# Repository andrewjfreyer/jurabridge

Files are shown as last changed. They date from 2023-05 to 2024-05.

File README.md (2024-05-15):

# jurabridge ☕

# TL;DR

An [ESP32 dev board](https://github.com/andrewjfreyer/jurabridge/wiki/Hardware) coupled to the service port of a [Jura ENA Micro 90](https://us.jura.com/en/customer-care/products-support/ENA-Micro-90-MicroSilver-UL-15116) can (1) poll machine data (e.g., sensors, memory, settings) via UART and (2) issue commands to the machine so as to act as a bridge between the machine and Home Assistant. See here for [hardware](https://github.com/andrewjfreyer/jurabridge/wiki/Hardware) and [software](https://github.com/andrewjfreyer/jurabridge/wiki/software) requirements. [Connections are straightforward.](https://github.com/andrewjfreyer/jurabridge/wiki/Hardware#connection-diagram)

[Home Assistant Forum Link](https://community.home-assistant.io/t/jura-ena-micro-90-to-mqtt-bridge)

# Summary

ESP32 Arduino project for bridging a [Jura ENA Micro 90](https://us.jura.com/en/customer-care/products-support/ENA-Micro-90-MicroSilver-UL-15116) to home automation platforms via MQTT. A 3.3v to 5v level shifter is required between hardware UART of the ESP32 to the service port of the Jura. The ESP32 polls the Jura for status information via reverse-engineered Jura Service Port calls, calculates/determines device state and meta statuses and reports changes to an MQTT broker. Added custom preparation functionality via a separate input button.

<p align="center">
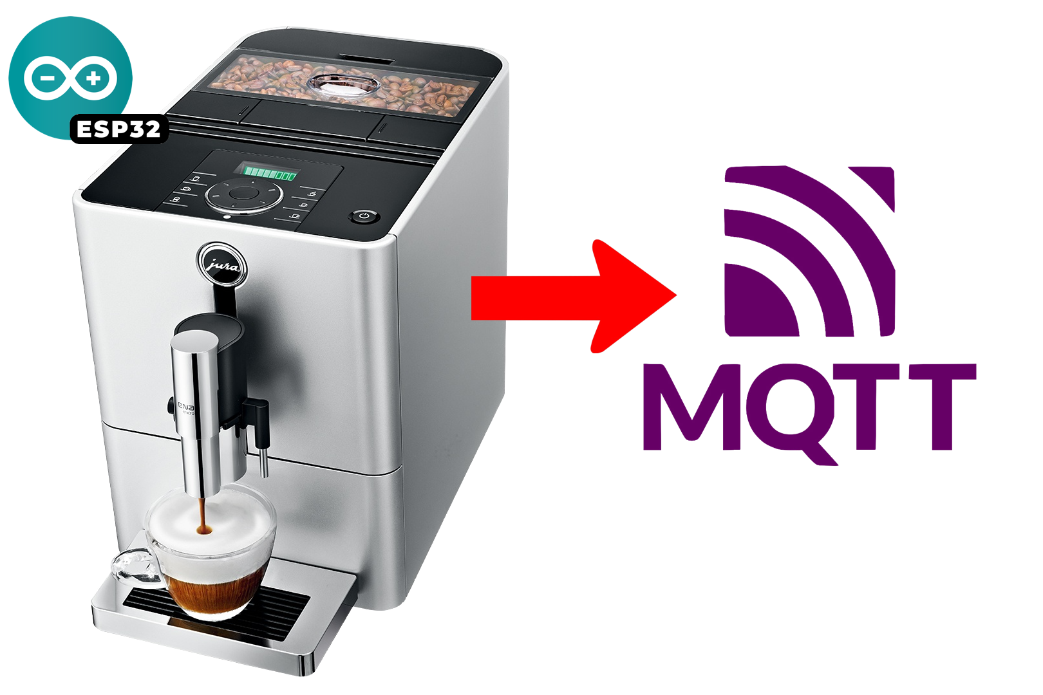
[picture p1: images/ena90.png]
Jura ENA Micro 90
  
</p>

# Why? It's a discontinued machine...

For fun, that's all. The machine is *awesome* and still available as a refurb. 

I saw [this](https://github.com/ryanalden/esphome-jura-component/) and other projects for other Jura models and thought I'd begin investigating the ENA Micro 90. Some existing comands worked, most did not. I needed to investigate and characterize a lot of the output from the machine and iterate through hundreds of commands to determine which ones the machine responded to, note what the response was, and then set about decoding/understanding what the data meant. One thing led to another, and now we're here. 

# So what? 

With 'jurabridge' we can/have: 

* ✅ **Power control.** Automatically turn the machine on and off in response to whatever triggers I want (via Home Assistant). Personally, mine is triggered from a motion sensor nearby the kitchen in the mornings. 

* ✅ **Custom coffee drinks.** Automatically create custom coffee or milk drinks with an arbitrary number of shots, arbitrary milk quantity, arbitrary water quantity (e.g., cortado, americano, lungo, ristretto, short cap, and so on). 

* ✅ **Tuning.** Fine-tune shots to improve quality. By default, the machine doses 8 - 9g of coffee (it seems) and pushes through it 30ml of water, which ends up being a 3:1 grounds to water dosing ratio. That's about half-strenth compared to a traditional pull. Also, after extraction starts, channeling is almost guaranteed to take over and extraction will suffer even before we consider how much water is being forced through. To improve shot quality then, we need to reduce water and/or increase coffee. We can't increase coffee because of torque limitations of the brew group drive motor during tamping. So our best option to improve our shot is to pull 15 - 17ml through a standard 8g puck twice, back-to-back. This would give about 30ml of espresso pulled through 16g of coffee, in aggregate. The shots are *much* better to my palate using this technique.

* ✅ **Quality control.** The thermoblock does not have fine temperture control, so there is quite a large range of possible extraction temperatures for different shots. The system can warn if the thermoblock is too high (meaning overextraction is likely), or if the thermoblock is too low (meaning underextraction is likely). In either case, running water through the machine can serve three purposes: (1) pre-warm a mug, (2) normalize thermoblock temperature below or around 100°C by purging heat or forcing the thermoblock on, and (3) clean the mug. This is not necessary in all cases, but is a good idea for best shot performance. 

* ✅ **Automation.** Automate our fine-tunings and/or temperature purge so that a perfect pull (sequence) executes without supervision.

* ✅ **Convenience & sanitation.** Automate maintenance operations such as brew group rinse and milk system rinse when the machine is idle. This will save internal silicon tubing from absorbing and accumulating burned coffee flavors, and it'll improve the sanitation of the milksystem.

* ✅ **Reminders.** Create maintence reminders or alerts via Home Assistant (e.g., iOS notifications, Alexa notifications, UI alerts or badges)

* ✅ **Alerts.** iOS alerts when a coffee product is ready.
  
* ✅ **Improved safety.** Ensure the machine turns off at an appropriate time, or in response to certain conditions. *⚠️ NOTE: If a milk clean operation is not completed and the machine is waiting for "water for milk clean," the thermoblock is held around 150 degrees celcius for sanitation purposes. There *DOES NOT* appear to be a timeout apart from the machine's power off timer, which may be on the order of hours. If the machine is left in this state, it'll consume signifiant power and pose a minor fire risk.*
  
* ✅ **Ridiculousness.** Due to the connection to Home Assisant, we have connection to voice assistants too: "Alexa, make me a short espresso." 

* ✅ **Overwhelming data.** We retreive all meters from the machine, including service life of the grinder, the drive motor of the brew group, and others. Can inform when other maintenance is necessary. 

# Table of Contents

### Reverse Engineering 

* [Jura ENA Micro 90 Command/Response Investigations & Interpretations](https://github.com/andrewjfreyer/jurabridge/wiki/Jura-Ena-Micro-90-Commands-v2)

* [Relevant Schematics](https://github.com/andrewjfreyer/jurabridge/wiki/Schematic(s))

### Building & Programming the `jurabridge`

* [Required & Optional Hardware](https://github.com/andrewjfreyer/jurabridge/wiki/Hardware)

* [Arduino Setup & Upload](https://github.com/andrewjfreyer/jurabridge/wiki/Software)

### Using `jurabridge` for Stuff

* [MQTT Topics & Payloads](https://github.com/andrewjfreyer/jurabridge/wiki/MQTT-Topics-v2)

* [Jura ENA Micro 90 Mods](https://github.com/andrewjfreyer/jurabridge/wiki/Jura-Ena-Micro-90-Modifications)

### Acknowledgements & Further Reading

* [References](https://github.com/andrewjfreyer/jurabridge/wiki/References)

# Home Assistant

The bridge automatically reports back to HA via MQTT Discovery, divided into a number of different devices for readability. Once `secrets.h` is configured with appropriate values, and device discovery finishes, size different devices will appear:

<p align="center">
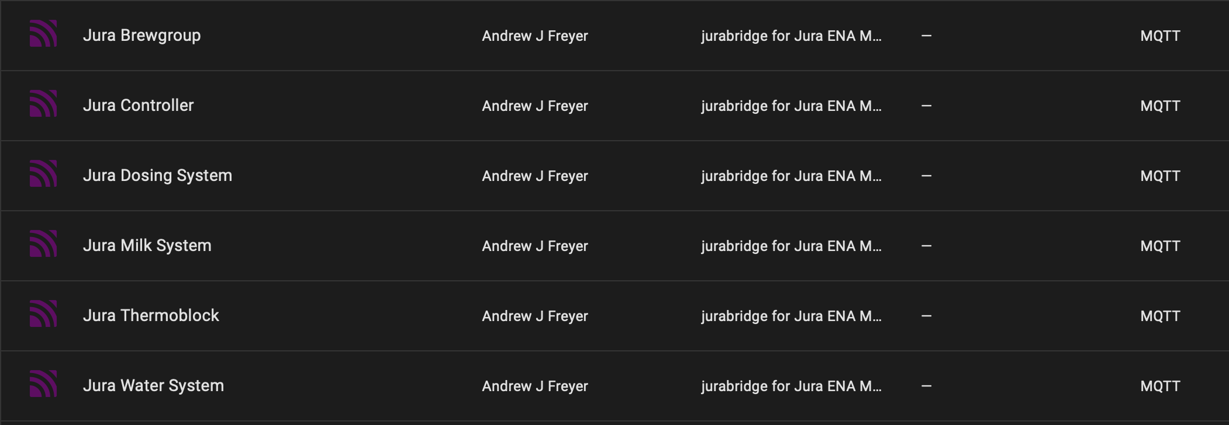
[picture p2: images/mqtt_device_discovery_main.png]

</p>

## Main Controller
<p align="center">
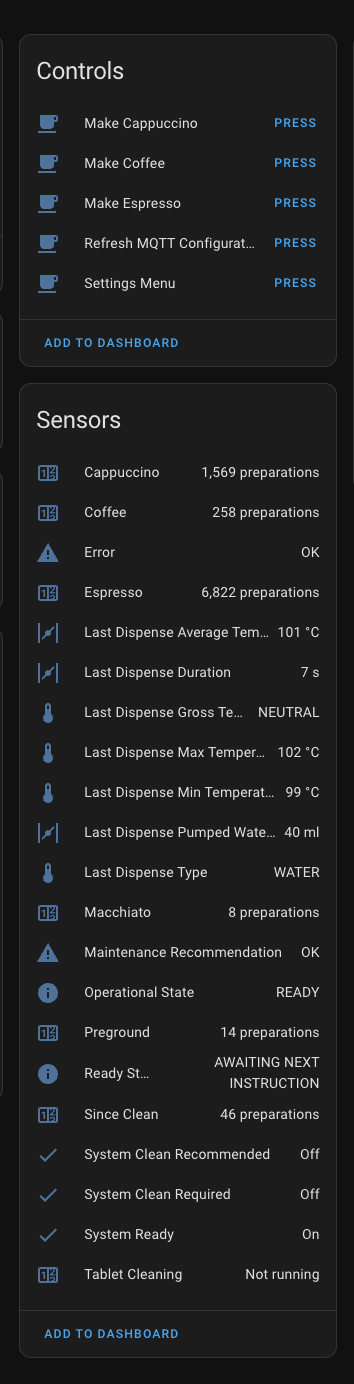
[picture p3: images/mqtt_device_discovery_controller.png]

</p>

## Brew Group
<p align="center">
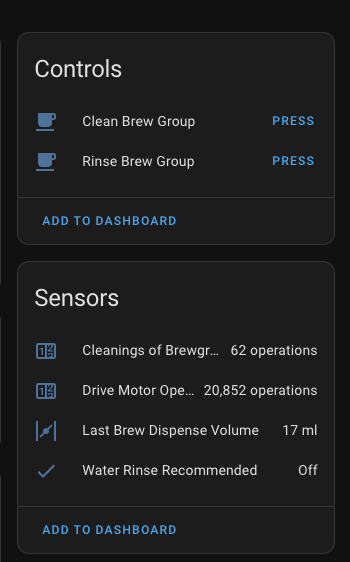
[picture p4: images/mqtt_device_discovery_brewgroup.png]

</p>

## Dosing System
<p align="center">
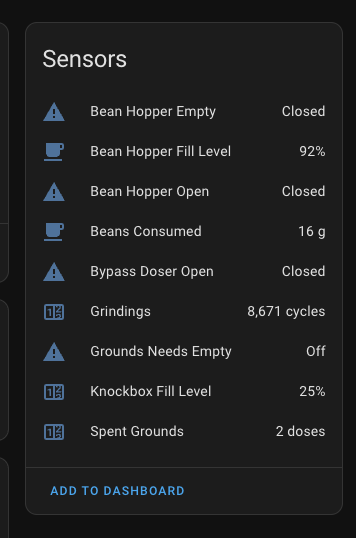
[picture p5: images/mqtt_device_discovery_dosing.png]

</p>

## Milk System
<p align="center">
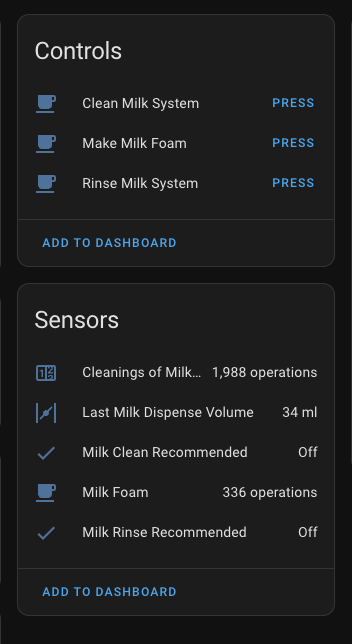
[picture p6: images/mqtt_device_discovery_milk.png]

</p>

## Water System
<p align="center">
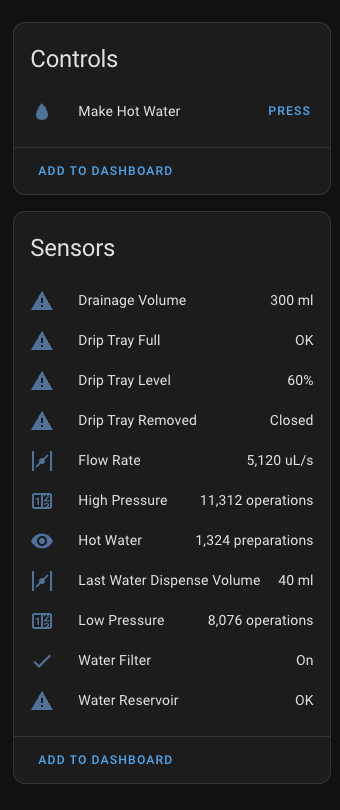
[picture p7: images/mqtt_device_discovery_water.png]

</p>

## Thermoblock
<p align="center">
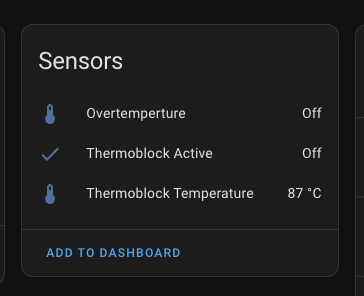
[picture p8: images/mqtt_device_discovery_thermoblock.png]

</p>

## User Interface Example

With all the automatically-exposed sensors, a UI can be built for Home Assistant that provides tons of information about the machine and its preparations. For example, with [button-card](https://github.com/custom-cards/button-card) and others: 

<p align="center">
  Jura Ena Micro 90
</p>

# `jurabridge` Hardware

Here is what the `jurabridge` looks like, attached to the machine after a few destructive [modifications](https://github.com/andrewjfreyer/jurabridge/wiki/Jura-Ena-Micro-90-Modifications) to feed a ribbon cable through the housing to the debug port. 

<p align="center">
  Jura Ena Micro 90
</p>

<p align="center">
  Jura Ena Micro 90
</p>

In v2, I added a momentary pushbutton to Pin 21 that allows for custom menus that leverage the machine's own display:

<p align="center">
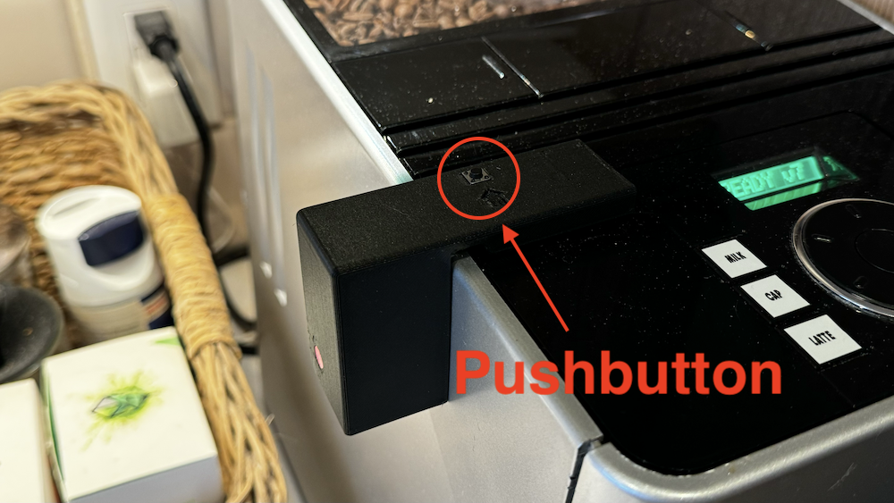
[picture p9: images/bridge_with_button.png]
  
</p>

The data output from the machine is received and presented by [Home Assistant presented via MQTT Device Discovery.](https://www.home-assistant.io) 

<hr/>

# Maintenance Automation

With machine status accurately known by the `jurabridge`, we can schedule maintenance operations automatically. This will increase output quality and sanitation to an extent. All this means is that a few minutes after a milk preparation has been completed and the machine has been idle, milk rinse is automatically performed. Similarly, after sitting idle for a time period, a water rinse is automaticaly performed. 

<hr/>

# Custom Preparations & Actions

I've found out that the default programming dramatically undersells the machine's capabilities. The Jura produces good enough shots as is. All that to say, since I bought the machine, my expectation was set that "this is the best it can do, and that's just fine." It is, after all, a superauto and sacrifies are made over a manual process. We're sacrificing some quality for pushbutton convenience. However, surprising to me was that the ENA Micro 90 only uses ***7-10g of coffee per perparation*** - with 30 some-odd ml of water. That's less coffee and more water than I presumed, without giving it much thought. Plus, pump pressure drops pretty dramatically due to channeling so, the first parts of our shots are the best parts anyway. 

It's of course easy to pull two short shots back to back to get to a more traditional 15 - 20g "single" shot, but why not automate it? 
Lets just automate it. Here, because `jurabridge` obtains (and/or infers) accurate machine status information, any number of custom recipes or custom instruction sequences can be excuted, without needing to modify EEPROM or to orchestrate a valid sequence of `FN:` commands, or without waiting for unnecessary long delays to presuming machine state. This command+interrupt+statuswait technique ensures that the machine excutes its own in-built sequences, and there's no risk of incidentally damaging the brewgroup with custom instructions or custom brew sequences. 

In this project there's a header above that defines custom functions that are accessible via a pushbutton. As an example, there are three custom operations defined. 

Each of the menu array entires conform to a struct: 

```

struct JuraCustomMenuItemConfiguration {
  const char name[255];
  const char topic[255];
  const char payload[255];
};

```

The name field of this struct should be ten ASCII characters or less, as this will be displayed on the machine's display. The array itself can be modified to include as many custom functions as needed:

```
static const JuraCustomMenuItemConfiguration JuraCustomMenuItemConfigurations[] {
  {
    " RISTR x2",
    MQTT_ROOT MQTT_SUBTOPIC_FUNCTION "make_espresso",
    "{'add':1,'brew':17}",
  },
  {
    "  CAP +1",
    MQTT_ROOT MQTT_SUBTOPIC_FUNCTION "make_cappuccino",
    "{'milk':60,'brew':17,'add':1}",
  },
  {
    "CORTADO +1",
    MQTT_ROOT MQTT_SUBTOPIC_FUNCTION "make_cappuccino",
    "{'milk':30,'brew':17',add':1}",
  },
  { /* the last element will always be treated as an exit, regardless the command phrase here */
    "   EXIT",
    "",
    "",
  }
};
```

<p align="center">
  Jura Ena Micro 90
</p>

1. The first index prepares a double ristretto in which two espresso shots are pulled back to back, each limited to 17ml of espresso output (that's about 2:1 ratio in respect of the grounds volume of 8g). 

2. The second index here prepares a cappuccino with 60ml of milk, 17ml of espresso, plus a second added shot of 17ml of espresso. 

3. The third index here prepares a "cortado" with 30ml of milk, 17ml of espresso, plus a second added shot of 17ml of espresso.

4. The final operation will cause the secret menu to close. The menu will time out after a short period of time as well. 15 seconds by default. 

To add other options, simply insert a new array item. For example, a two-shot americano: 

```
{
  " AMERI x2",
  MQTT_ROOT MQTT_SUBTOPIC_FUNCTION "make_hot_water",
  "{'add':2,'brew':17}",
}
```

Or a lungo:

```
{
  "  LUNGO",
  MQTT_ROOT MQTT_SUBTOPIC_FUNCTION "make_espresso",
  "{'brew':40}",
}
```

In other cases, you can define your own personal brew preferences that will apply to the next physical button press of the machine. In the following example, pressing any of the program buttons will cause the next button press to limit brew output volume to 17 ml.

```
{
  "ESPRESSO 1",
  MQTT_ROOT MQTT_DISPENSE_CONFIG,
  "{'brew':17}",
}
```

Or, simply add a shot to any other preparation. In this case, we can automatically add a 17ml espresso pull after any other machine button. After enabling this option, the display will update to "PRODUCT?", encouraging selection of one of the six prefab buttons (espresso, cappuccino, macchiato, water, milk foam, coffee). Once the use makes a selection and the selected program completes, a shot will be pulled:

```
{
  " ADD SHOT",
  MQTT_ROOT MQTT_DISPENSE_CONFIG,
  "{'add':1,m 'brew':17}",
}
```
<hr/>

# Functions & Buttons in Home Assistant

The [JuraConfiguraton.h](https://github.com/andrewjfreyer/jurabridge/blob/main/v2/JuraConfiguration.h) header lists what buttons are reportable to home assistant. By default, most are disabled as each additional sensor adds reporting time and cycle time. 

## Disclaimer

*This repository is only provided as information documenting a project I worked on for kicks. No warranty or claim that this will work for you is made. I have described some actions that involve modifying a Jura ENA Micro 90, which if performed will absolutely void any warranty you may have (which you probably don't; this machine is old). Some of the modifications described below involve mains electricity; all appropriate cautions are expected to be, and were, followed. Some of these modifications are permanent and irreversible without purchasing replacement parts. Do not duplicate any of this project unless you know exactly what you are doing. I do not take **any** responsibility for any frustration, spousal irritation, bad coffee, injuries, or damage to your machine, your home plumbing, your home, or anyone or anything that may occur from any accident, lack of common sense or experience, poor planning, or following this project word for word. Responsibility for any effect, including damages or distress, resulting from reliance on any information made available here is not the responsibility of the author or other contributors. All rights are reserved.*

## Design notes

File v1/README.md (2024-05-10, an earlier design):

> ⚠️ **DEPRECATION WARNING:** This entry relates to v1 of this project and has been deprecated/updated as of [v2](https://github.com/andrewjfreyer/jurabridge/tree/main/v2). 

# jurabridge v1 ☕

# Description

This is an ESP32 Arduino project for bridging a [Jura ENA Micro 90](https://us.jura.com/en/customer-care/products-support/ENA-Micro-90-MicroSilver-UL-15116) to home automation platforms via MQTT. Main controller is an ESP32. A 3.3v to 5v level shifter is required between an available hardware UART of the ESP32 to the debug/service port of the Jura. Don't use `softwareserial`, as it's painfully slow. The ESP continually polls the Jura for status information, and reports changes in status information via MQTT. 

See here for [hardware](https://github.com/andrewjfreyer/jurabridge/wiki/Hardware) and [software](https://github.com/andrewjfreyer/jurabridge/wiki/software) requirements. [Connections are straightforward.](https://github.com/andrewjfreyer/jurabridge/wiki/Hardware#connection-diagram)

<p align="center">
  Jura ENA Micro 90
</p>

# Why?

I saw [this](https://github.com/ryanalden/esphome-jura-component/) and other similar projects and thought I'd begin investigating whether some or all of the functionality would extend to the Jura ENA Micro 90. Many did, many did not. I needed to investigate and characterize a lot of the output from the machine. One thing led to another, and now we're here.

# Table of Contents

### Reverse Engineering 

* [Jura ENA Micro 90 Command/Response Investigations & Interpretations](https://github.com/andrewjfreyer/jurabridge/wiki/Jura-Ena-Micro-90-Commands)

* [Relevant Schematics](https://github.com/andrewjfreyer/jurabridge/wiki/Schematic(s))

### Building & Programming the `jurabridge`

* [Required & Optional Hardware](https://github.com/andrewjfreyer/jurabridge/wiki/Hardware)

* [Arduino Setup & Upload](https://github.com/andrewjfreyer/jurabridge/wiki/Software)

### Using `jurabridge` for Stuff

* [MQTT Topics & Payloads](https://github.com/andrewjfreyer/jurabridge/wiki/MQTT-Topics)

* [Home Assistant Configuration Example](https://github.com/andrewjfreyer/jurabridge/wiki/Home-Assistant-Configuration)

* [Jura ENA Micro 90 Mods](https://github.com/andrewjfreyer/jurabridge/wiki/Jura-Ena-Micro-90-Modifications)

* [Custom Preparation Scripts](https://github.com/andrewjfreyer/jurabridge/wiki/Custom-Recipe-Scripts)

### Acknowledgements & Further Reading

* [References](https://github.com/andrewjfreyer/jurabridge/wiki/References)

# Home Assistant

Here's my Home Assistant [configuration (YAML package)](https://github.com/andrewjfreyer/jurabridge/wiki/Home-Assistant-Configuration). Here is what the bridge looks like, attached to the machine after a few destructive [modifications](https://github.com/andrewjfreyer/jurabridge/wiki/Jura-Ena-Micro-90-Modifications) to feed a ribbon cable to the debug port. 

<p align="center">
  Jura Ena Micro 90
</p>

<p align="center">
  Jura Ena Micro 90
</p>

Here's a quick video demo showing the responsiveness of the polling:

<div align="center">
      <a href="https://youtu.be/6NN9Xv9Lhq4">
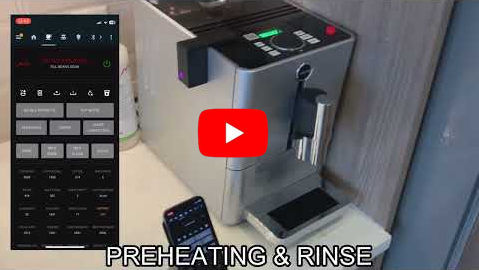
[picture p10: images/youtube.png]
         
      </a>
</div>

The data output from the machine is received and presented by [Home Assistant.](https://www.home-assistant.io) I have created this status UI based on a modified fork of [button-card](https://github.com/custom-cards/button-card). 

<p align="center">
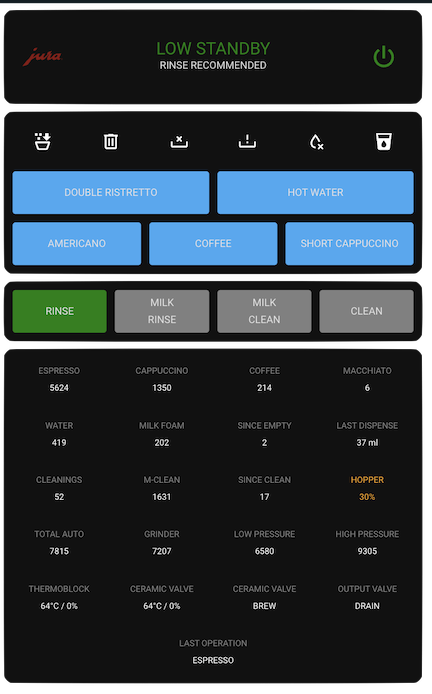
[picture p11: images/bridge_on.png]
BridgeOn
  
</p>

*Note: Although loosely compatible, this code is far too large to work with ESPHome; attempts to get it to work usefully with all sensors updating at reasonable intervals caused watchdog crashes.*

<hr/>

# Custom Preparations & Actions

I've found out that the default programming of the machine undersells/underutilizes machine's capabilities. The Jura produces good enough shots as is. I never thought to question the dosing volume, as the output was good enough for what I expected from a superautomatic. 

All that to say, since I bought the machine, my expectation was set that "this is the best the Jura can do, and that's just fine." It is, after all, a superauto. We're sacrificing some quality for pushbutton convenience. However, somewhat surprising to me was that the ENA Micro 90 only uses ***7-10g of coffee per perparation*** - about half as much as I presumed. 

It's of course easy to pull two shots back to back to get to a more traditional 15 - 20g per pull. But that requires that I sit and wait, read words on a display, clear any errors, and press buttons twice. Who has time for that?

Lets just automate it. 

Here, because `jurabridge` obtains (and/or infers) accurate machine status information, any number of custom recipes or custom instruction sequences can be excuted, without needing to modify EEPROM or to orchestrate a valid sequence of `FN:` commands, or without waiting for unnecessary long delays and presuming machine state. This command+interrupt+statuswait technique ensures that the machine excutes its own in-built sequences, and there's no risk of incidentally damaging the brewgroup with custom instructions or custom brew sequences. 

Custom sequences/scripts can be made to allow the machine to produce a wide variety of other drinks, at higher quality. As a trivial example, different settings may be appropriate for non-dairy cappuccino than dairy cappuccino, yet the machine only has one setting. 

[Custom recipe examples.](https://github.com/andrewjfreyer/jurabridge/wiki/Custom-Recipe-Scripts)

<hr/>

## Disclaimer

*This repository is only provided as information documenting a project I worked on. No warranty or claim that this will work for you is made. I have described some actions that involve modifying a Jura ENA Micro 90, which if performed will void any warranty you may have. Some of the modifications described below involve mains electricity; all appropriate cautions are expected to be, and were, followed. Some of these modifications are permanent and irreversible without purchasing replacement parts. Do not duplicate any of this project unless you know exactly what you are doing. I do not take anyresponsibility for any frustration, spousal irritation, bad coffee, injuries, or damage to your machine, your home plumbing, your home, or anyone or anything that may occur from any accident, lack of common sense or experience, poor planning, or following this project word for word. Responsibility for any effect, including damages or distress, resulting from reliance on any information made available here is not the responsibility of the author or other contributors. All rights are reserved.*

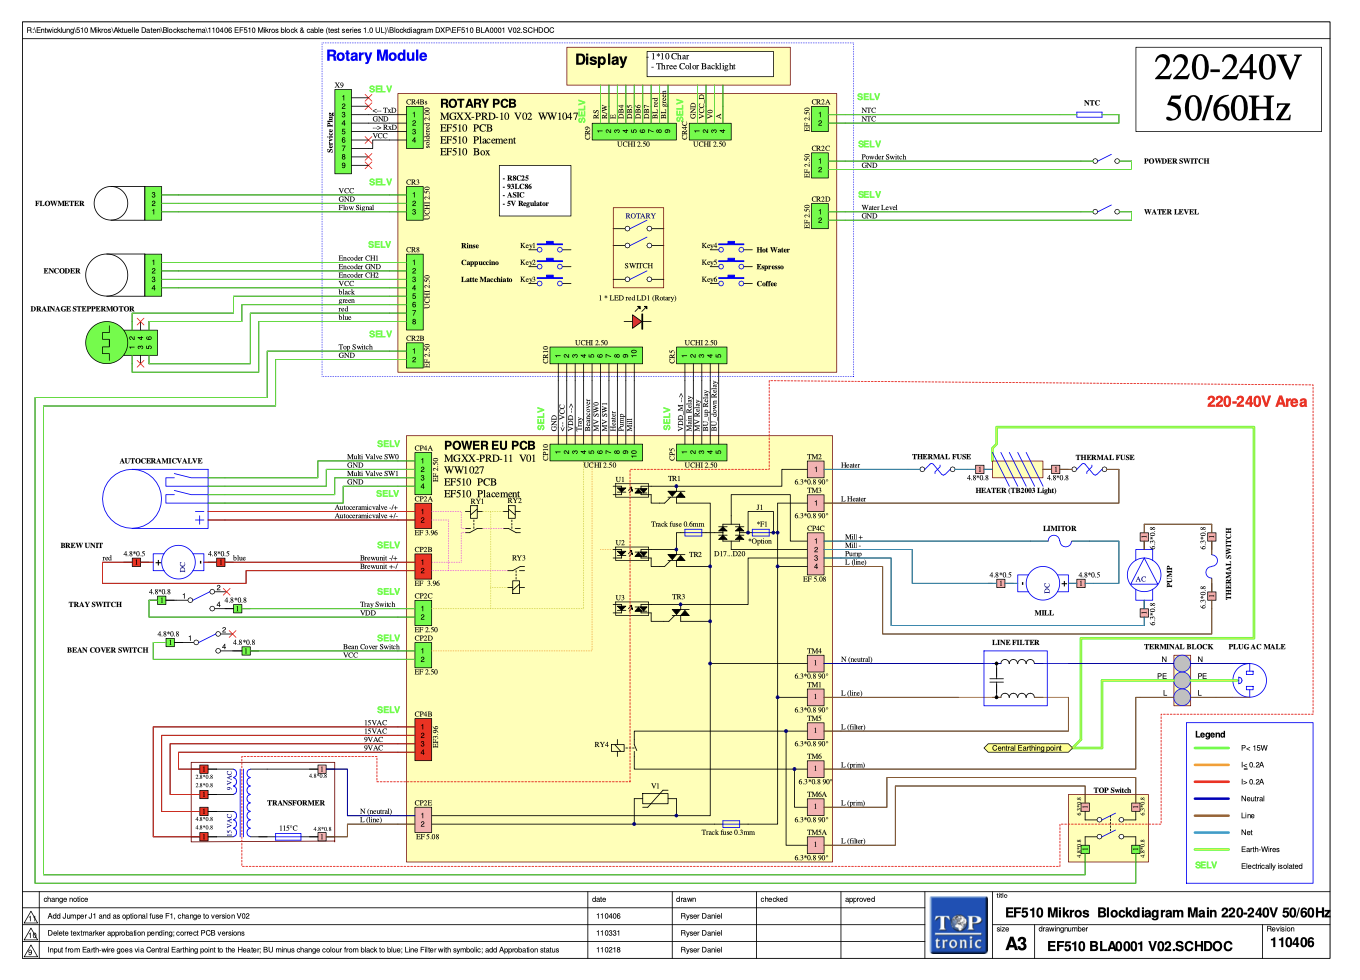
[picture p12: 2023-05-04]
images/schematic_micro9.png

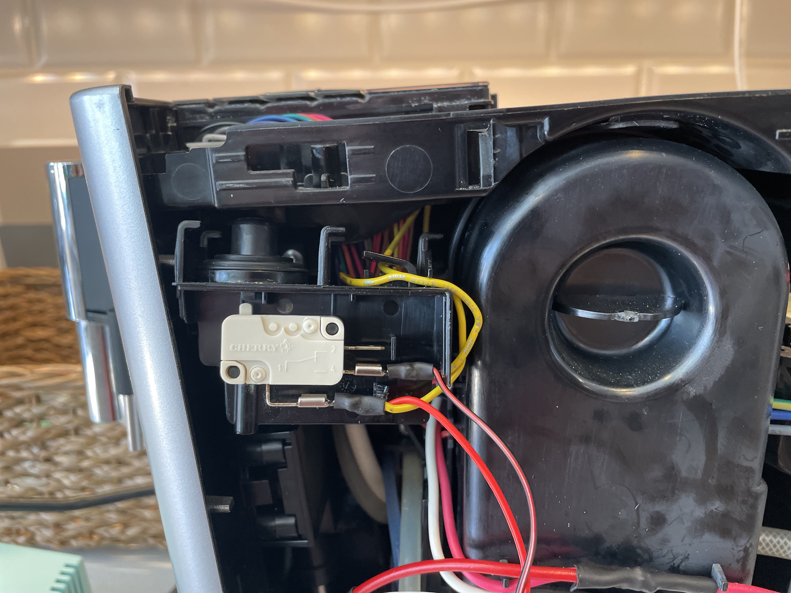
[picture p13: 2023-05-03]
images/lv_splice.jpg

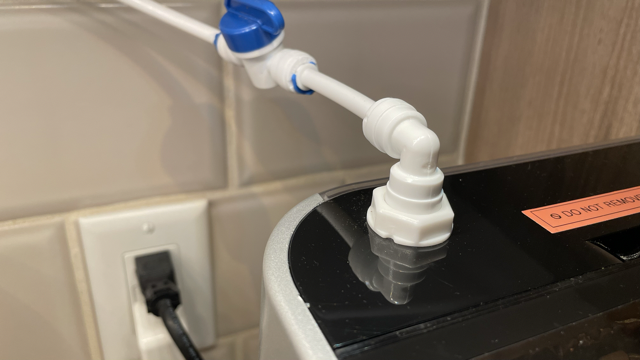
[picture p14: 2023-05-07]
images/plumb-connection.png

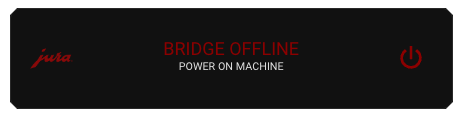
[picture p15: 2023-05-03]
images/bridge_off.png

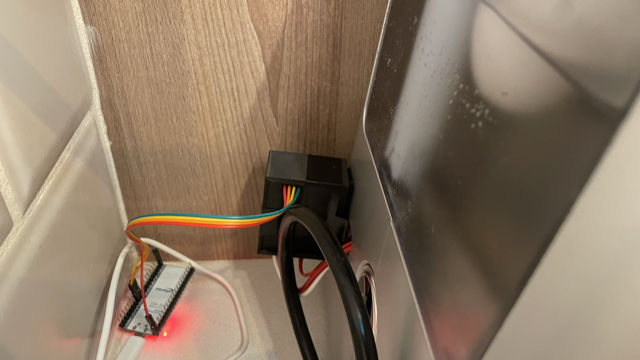
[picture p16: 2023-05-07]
images/plumb-controller.png

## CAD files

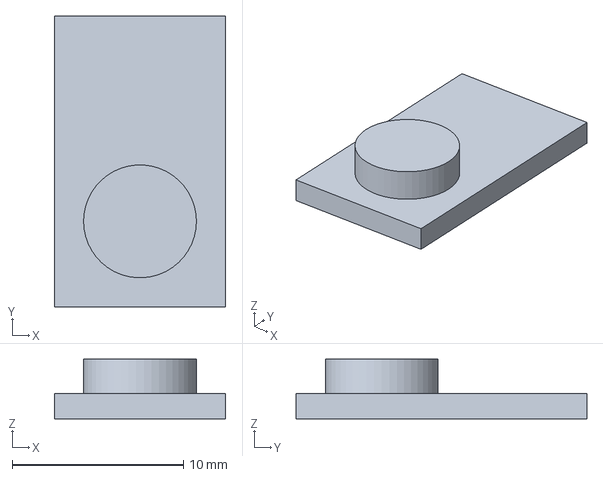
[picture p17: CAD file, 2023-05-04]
models/jurabridge-diffuser.3mf
10.0 x 17.0 x 3.50 mm

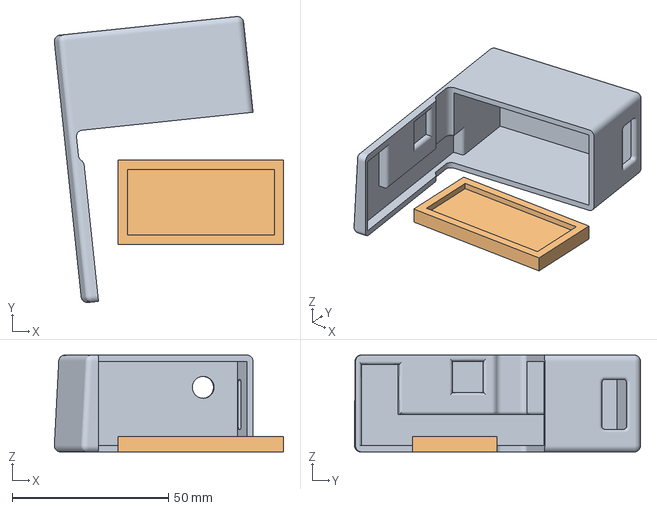
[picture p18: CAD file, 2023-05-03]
models/jurabridge.3mf
73.4 x 91.5 x 31.0 mm
JuraDebugPort v7
JuraDebugPort -holder v8

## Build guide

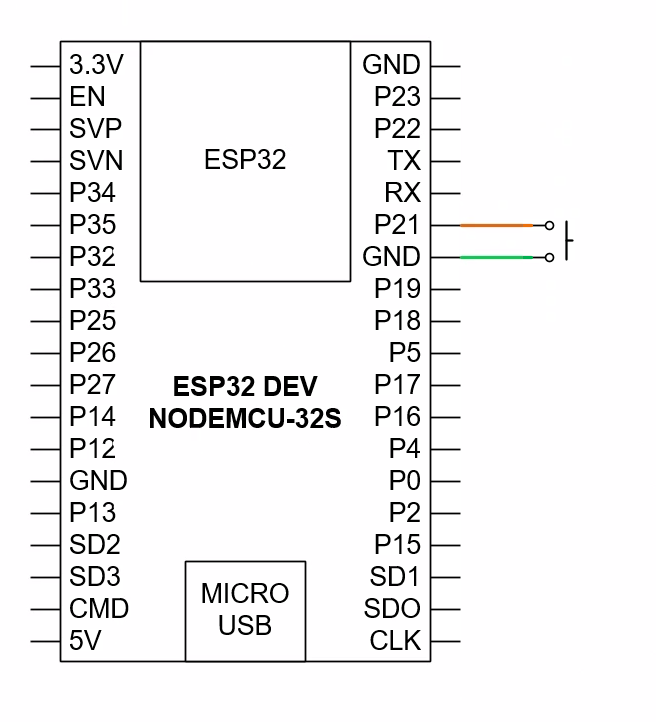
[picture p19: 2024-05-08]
images/wiring_button.png

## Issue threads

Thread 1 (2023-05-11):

Sensor range max/min to prevent unexpected errors

andrewjfreyer, 2023-05-11:
Calculated sensors can provide very unexpected results, briefly, before correcting. Simple ranges will fix.

Example: estimated hopper volume

andrewjfreyer, 2023-05-11:
0.4.29

Closed 2023-05-11.

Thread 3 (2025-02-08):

WiFi Problem

martin1neu, 2025-02-08:
Hello Andrew,

really great project - my admiration for all the time you've put into it.

I would also like to realize the project, sketch upload works (Arduino IDE 2.3.4). Unfortunately I can't get a wifi connection.
I have also tried it with 2 different boards (WEMOS Lolin32 & Geekworm Easy Kit ESP32-C1) - same problem.

the secrets.h should actually fit:

#ifndef SECRETS_H
#define SECRETS_H

#define WIFINAME “wifi_name”
#define WIFIPASS “numbers_and_!”
#define MQTTBROKER “IP_mqttbroker”
#define MQTT_PASS “”
#define MQTT_USER “username”
#endif

the ArduinoIDE example “SimpleWifiServer” works.

Do you have any ideas here?

Many thanks in advance
greetings from austria - martin

martin1neu, 2025-02-10:
Hello Andrew,

thanks again for your work, but I have now implemented the project with “IoT-Enabled-Coffee-Machine” and therefore don't need any more help.

best regards from Austria

martin

andrewjfreyer, 2025-03-11:
Hi Martin,

Apologies for missing this issue report. I would bet that you were either running into hardware limitations of your chosen board. I had lots of problems finding a board with appropriate resources for both the UART looping and the  mqtt, and wifi packages.

Best,

Andrew

martin1neu, 2025-03-12:
Hi Andrew,

thanks a lot for answer (you make this in your free-time and so i think that every answer is very helpfull, especially for others in future time)
Hardware limitation is in general a problem. I see it also at my current project for reading out 2 smartmeters.

regards martin

Closed 2025-02-10.

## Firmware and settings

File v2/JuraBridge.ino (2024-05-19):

/* external library requirements */
#include "Preferences.h"
#include "PubSubClient.h"
#include "ArduinoJson.h"
#include <WiFi.h>
#include <string>

/* project requirements */
#include "Secrets.h"
#include "Version.h"
#include "JuraMachine.h"
#include "JuraBridge.h"
#include "JuraCustomMenu.h"

/* macros */
#define xSemaphoreWrappedSetBoolean(x,y,z)  xSemaphoreTake(x, portMAX_DELAY ); y = z; xSemaphoreGive(x);
#define vTaskDelayMilliseconds(x)  vTaskDelay(pdMS_TO_TICKS(x));

/* nvs preferences handler */
Preferences prefs;

/* need to stop long-run tasks when MQTT signaling is required */
SemaphoreHandle_t xUARTSemaphore; 

/* need to ensure that different tasks do not call the mqtt client at the same time; */
SemaphoreHandle_t xMQTTSemaphore; 
SemaphoreHandle_t xMQTTStatusSemaphore; 
SemaphoreHandle_t xWIFIStatusSemaphore; 
SemaphoreHandle_t xMachineReadyStateVariableSemaphore; 

/* define comms */
WiFiClient wifiClient;
PubSubClient mqttClient(wifiClient);

/* define machine instance */
JuraBridge bridge(prefs, mqttClient, xMQTTSemaphore, xUARTSemaphore);
JuraMachine machine(bridge, xMachineReadyStateVariableSemaphore);

/* task handles */
TaskHandle_t xUART, xLED;

/* queue */
QueueHandle_t xQ_SubscriptionMessage; // payload and topic queue of MQTT payload and topic
const int payloadSize = 512;
struct mqtt_message {
  char payload [payloadSize] = {'\0'};
  String topic ;
} rx_message;

/* protected state variables */
volatile bool connectedToBroker;
volatile bool connectedToNetwork;

/* button */
struct Button {
	bool released;
  bool isBeingHeld;
  unsigned long startat;
  unsigned long endat;
};

/* custom menu object */
struct JuraCustomMenu {
	unsigned int item;
	bool active;
  unsigned long time;
};

volatile Button menuButton = {false, false, 0, 0};
volatile JuraCustomMenu customMenu = {0, false, 0};

//variables to keep track of the timing of recent interrupts

/***************************************************************************//**
 * Loop task to iteratively poll machine via UART
 *
 * @param[out] null 
 *     
 * @param[in] pvParameters required for callback
 ******************************************************************************/
void machineStatePollingHandler (void * pvParameters){

  /* await broker connection */
  while (!connectedToBroker){
    vTaskDelayMilliseconds(500);
  }
  
  /* get innitial properties before polling starts y! */
  initJuraEntityStatesFromNonVolatileStorage();


  int loopIterator = 1; 
  for(;;){ 
    /*

      00-0F :   8400 0023 D4D4 487C 0103 0000 0011 0000 0A3A 259B 064F D09D 719F 2DCF 01FF 3BB6
      10-1F :   E2E2 E2E2 E2E2 D5D5 D5D5 D5D5 D5D5 D5D5 D5D5 D5D5 D5D5 D5D5 D5D5 D5D5 D5D5 D5D5 <- last D5D5s all appear to change for button presses on the rotary
        Center Button: N - 4
        Right: N - 1?
        Left:  N + 1?

      20-2F :   0000 0000 0000 0000 40EB 7224 000A 0C72 7218 C2F5 74F3 FFFF 0000 0000 0000 0000
      30-3F :   0000 0000 0000 0000 0000 0000 0000 0000 0000 0000 0000 0000 0000 0000 0000 0000 
      40-4F :   0000 0707 0200 0023 9201 9C00 07D9 00CA 0408 0001 0001 1600 EB7C 0450 C272 2C6A
      50-5F :   B70E 0752 C1C2 FD00 FB0F AB72 046E 0AFE F908 730D CF75 012C 0080 0404 F2FE D108
      60-6F :   126E 821A 030C 0906 04F2 F500 3558 00AD 73FA 245D FFC0 1FC9 6A10 0072 2308 0FB0
      70-7F :   FD07 4A02 0642 FF05 4042 5A15 00AF 0008 2CB5 D800 6E29 FD00 4764 00EB D800 5BBE
      80-8F :   6E48 7505 03FF E314 7504 D923 45A1 0762 0020 F5FE 01F9 47B5 FEFD 0BFF FFFF 6A02
      90-9F :   FD00 7EE4 045A AEFE 0173 9F7E CF75 FF0A C2E2 6A1A CB75 F7E2 7306 FDDD 0020 7303
      A0-AF :   B23C FEC1 73F3 400B 7309 046E 046A 6E73 00E2 066E 0AE7 B708 F272 03D8 507D FFBE
      B0-BF :   D84E 7C00 4B75 C175 2746 086C 0BBF 6E04 F500 3273 75E5 C900 BF7E 7D00 FE8B FFFF
      C0-CF :   40EB 0053 3C50 2CF2 5D00 F502 4CEA FDB1 FD0B 76F2 FD00 0BF3 0173 F507 F500 F36E
      D0-DF :   4003 03F5 ACCE 4CF8 5909 07C8 7300 B0A1 00AA 00DD 0564 7407 0B1D 7E24 3A5C C1F2
      E0-EF :   68FF FFFF FFFF FFFF FFFF FFFF FFFF FFFF FFFF FFFF FFFF FFFF FFFF FFFF FFFF FFFF
      F0-FF :   FFFF FFFF FFFF FFFF FFFF FFFF FFFF FFFF FFFF FFFF FFFF FFFF FFFF FFFF FFFF FFFF
    */

    if (!customMenu.active){
      machine.handlePoll(loopIterator);
      loopIterator = (loopIterator % 100) + 1; 
      vTaskDelayMilliseconds(10);
    }else{
      vTaskDelayMilliseconds(500);
    }
  }
}


/***************************************************************************//**
 * Await the machine ready state then add a shot 
 *
 * @param[out] null 
 *     
 * @param[in] addShot int number of shots
 * @param[in] brewLimt int limit for brew out
 ******************************************************************************/
void awaitDispenseCompletionToAddShots( int addShot = 1, int brewLimit = 17 ){

  /* precharge the wait display for between elements */
  bridge.instructServicePortToDisplayString("   WAIT   ");

  /* iterating over two shots */
  for( int shot = 0; shot < addShot; shot ++){

    /* define a non-ready state that is not processed in the machine poller; protect  */
    machine.startAddShotPreparation();
    /* 
      NOTE TO READER: intentionally leave the semaphore taken here to prevent a ready state from happen
      until we get into the while loop below; 
    */

    /* entire the loop before returning the semaphore */
    xSemaphoreTake( xMachineReadyStateVariableSemaphore, portMAX_DELAY );
    
    bool canGiveSemaphore = true;
    while (machine.states[(int) JuraMachineStateIdentifier::SystemIsReady] == false){
      vTaskDelayMilliseconds(500);
      if (canGiveSemaphore){
        xSemaphoreGive( xMachineReadyStateVariableSemaphore);
        canGiveSemaphore = false;
      }
    }

    /* between different shots - resting period */              
    vTaskDelayMilliseconds(2500);

    /* set brew limit here */
    machine.setDispenseLimit(brewLimit, JuraMachineDispenseLimitType::Brew) ;

    /* send the command for this repetition */
    bridge.instructServicePortWithJuraFunctionIdentifier(JuraFunctionIdentifier::MakeEspresso);

    /* resting period */              
    vTaskDelayMilliseconds(2500);
  }
}

/***************************************************************************//**
 * Process singe-item queue here so as to offload processing of mqtt
 * message content from the mqtt callback itself.
 * 
 * notes: design pattern based on @idahowalker on arduino.cc forums
 *
 * @param[out] null 
 *     
 * @param[in] pvParameters required for callback
 ******************************************************************************/
void receivedMQTTMessageQueueWorker( void *pvParameters ){
  /* processing message px_message differs from received message rx_message */
  struct mqtt_message px_message;
  for (;;)
  {
    /* wait until the message queue includes something; */
    if ( xQueueReceive(xQ_SubscriptionMessage, &px_message, portMAX_DELAY) == pdTRUE ){
      String mqttMessageString = String(px_message.payload);
      String topic = String(px_message.topic);
      int brewLimit = 0;
      int addShot = 0;
      int milkLimit = 0; 
      int waterLimit = 0;

      /* was this a json string?  */
      if (mqttMessageString.length() > 0){

        /* define static; will this leak memory? */
        StaticJsonDocument<1024> receivedJson ;
        DeserializationError json_deserialization_error = deserializeJson(receivedJson, (const char*) mqttMessageString.c_str());
        
        /* reset all */
        machine.resetDispenseLimits();
        
        /* if the message aws JSOn and included properly formatted dictionary, then set the limits; reset on failure?*/
        if (! json_deserialization_error) {
          JsonObject dictObjct = receivedJson.as<JsonObject>();
          if (dictObjct.containsKey("milk")){
            machine.setDispenseLimit( (int) dictObjct["milk"],JuraMachineDispenseLimitType::Milk) ;
            milkLimit =  (int) dictObjct["milk"];
          }
          if (dictObjct.containsKey("brew")){
            machine.setDispenseLimit( (int) dictObjct["brew"],JuraMachineDispenseLimitType::Brew) ;
            brewLimit = (int) dictObjct["brew"];
          }
          if (dictObjct.containsKey("water")){
            machine.setDispenseLimit( (int) dictObjct["water"],JuraMachineDispenseLimitType::Water) ;
            waterLimit =  (int) dictObjct["water"];
          }
          if (dictObjct.containsKey("add")){
            addShot = (int) dictObjct["add"];
            addShot = addShot > 2 ? 2 : addShot < 0 ? 0 : addShot;
          } 
          /* is this a straigh up dispense config? */
          if (topic == MQTT_ROOT MQTT_DISPENSE_CONFIG) {
            bridge.instructServicePortToDisplayString(" PRODUCT?");
            
            /* if addshot is set, we need to wait for non-*/
            if (addShot > 0){

              /* entire the loop before returning the semaphore */
              bool canGiveSemaphore = true;
              while (machine.states[(int) JuraMachineStateIdentifier::SystemIsReady] == true){
                vTaskDelayMilliseconds(500);
                if (canGiveSemaphore){
                  canGiveSemaphore = false;
                }
              }

              /* define a non-ready state that is not processed in the machine poller; protect  */
              machine.startAddShotPreparation();

              /* instruct add shots */
              awaitDispenseCompletionToAddShots(addShot, brewLimit);

              /* return to ready*/
              bridge.instructServicePortToSetReady();

            }else{
              ESP_LOGI(TAG,"Custom limits set: Water: %i ml Milk: %i ml Brew: %i ml", waterLimit, milkLimit, brewLimit);
              continue;
            }
          }
        }
      }

      /* --- First, process through known mqtt subscriptions  ---  */
      int functionEntityArraySize = sizeof(JuraMachineFunctionEntityConfigurations) / sizeof(JuraMachineFunctionEntityConfigurations[0]) ; 
      for (int i = 0; i < functionEntityArraySize; i++){

        /* find the topic among prefab functions?  */
        if (topic == JuraMachineFunctionEntityConfigurations[i].command_topic && 
            JuraMachineFunctionEntityConfigurations[i].command != JuraServicePortCommand::None){

          /* instruct the custom command */          
          bridge.instructServicePortWithCommand(JuraMachineFunctionEntityConfigurations[i].command);

          /* dealy */
          vTaskDelay(500 / portTICK_PERIOD_MS);

          /* add shot ? */
          if (addShot > 0) {
            
            /* debug */
            ESP_LOGI(TAG,"--> Machine Add Shot Function: %s", JuraMachineFunctionEntityConfigurations[i].name);
            awaitDispenseCompletionToAddShots(addShot, brewLimit);
          }

          /* set ready */
          bridge.instructServicePortToSetReady();
          break;
        }
      }

      /* --- machine topics and bridge topics  ---  */
      if (topic ==  MQTT_ROOT MQTT_SUBTOPIC_MENU) {

        /* enter settings menu */
        bridge.instructServicePortWithJuraFunctionIdentifier(JuraFunctionIdentifier::SettingsMenu);
        vTaskDelayMilliseconds(300);

        /* select first menu item */
        bridge.instructServicePortWithJuraFunctionIdentifier(JuraFunctionIdentifier::SelectMenuItem);
        vTaskDelayMilliseconds(300);

        //how far into the menu do we go?
        int menu_item = 99;

        if      (mqttMessageString ==  "mclean")  { menu_item = 0;}
        else if (mqttMessageString ==  "rinse")   { menu_item = 1;}
        else if (mqttMessageString ==  "mrinse")  { menu_item = 2;}
        else if (mqttMessageString ==  "clean")   { menu_item = 3;}
        else if (mqttMessageString ==  "filter")  { menu_item = 4;}

        /* correct menu! */
        if (menu_item < 5){
          //navigate to message 
          for (int i = 0; i < menu_item; i++){
            bridge.instructServicePortWithJuraFunctionIdentifier(JuraFunctionIdentifier::RotaryRight);
            vTaskDelayMilliseconds(300);
          }

          //press the selected button and be done with it
          bridge.instructServicePortWithJuraFunctionIdentifier(JuraFunctionIdentifier::SelectMenuItem);
          vTaskDelayMilliseconds(300);
        }

      } else if (topic == MQTT_ROOT MQTT_BRIDGE_RESTART) {
        ESP.restart();

      } else if (topic == MQTT_ROOT MQTT_CONFIG_SEND) {
        bridge.instructServicePortToDisplayString("   WAIT");
        bridge.publishMachineEntityConfigurations();
        bridge.publishMachineFunctionConfiguration(); 

        /* set ready */
        bridge.instructServicePortToSetReady();

      } else if (topic == HA_STATUS_MQTT) {
        if (mqttMessageString == "online"){
          ESP.restart();
        }
      }
    }
  }
}

/***************************************************************************//**
 * RAM held dumping and debug spot for Wifi events. Insert switch 
 * for debugging.
 * 
 * notes: design pattern based on @idahowalker on arduino.cc forums
 *
 * @param[out] null 
 *     
 * @param[in] WiFiEvent_t wifi event for preocessing
 ******************************************************************************/
void IRAM_ATTR WiFiEvent(WiFiEvent_t event){}

/***************************************************************************//**
 * RAM held mqtt rx event processor; dump received messages into 
 * single-item queue for processing at a later time. Structure message
 * into a single object that can be added into the xQueue
 * 
 * notes: design pattern based on @idahowalker on arduino.cc forums
 *
 * @param[out] null 
 *     
 * @param[in] topic char array pointer to topic of the rx message
 * @param[in] payload byte array pointer to payload of the rx message 
 * @param[in] length unsigned int length of the payload
 ******************************************************************************/
void IRAM_ATTR mqttCallback(char* topic, byte * payload, unsigned int length){
  memset( rx_message.payload, '\0', payloadSize ); // clear payload char buffer
  rx_message.topic = ""; //clear topic string buffer
  rx_message.topic = topic; //store new topic
  int i = 0; // extract payload
  for ( i; i < length; i++)
  {
    rx_message.payload[i] = (char)payload[i];
  }
  rx_message.payload[i] = '\0';
  xQueueOverwrite( xQ_SubscriptionMessage, (void *) &rx_message );// send data to queue
} 

/***************************************************************************//**
 * Second function for processing menu items with MQTT handler, but without 
 * requireing a bounce-0ff of the broker ( wifi disconnect is a problem... )
 *
 * @param[out] null 
 *     
 * @param[in] topic const char array pointer to topic of the rx message
 * @param[in] payload const char array pointer to payload of the rx message 
 * @param[in] length unsigned int length of the payload
 ******************************************************************************/
void IRAM_ATTR mqttCallbackBypassBroker(const char* topic, const char* payload, unsigned int length){
  memset( rx_message.payload, '\0', payloadSize ); 
  rx_message.topic = ""; 
  rx_message.topic = topic; 
  int i = 0; 
  for ( i; i < length; i++)
  {
    rx_message.payload[i] = (char)payload[i];
  }
  rx_message.payload[i] = '\0';
  xQueueOverwrite( xQ_SubscriptionMessage, (void *) &rx_message );// send data to queue
} 

/***************************************************************************//**
 * Publish device configuration to Home Assistant via configured broker. 
 *
 * @param[out] none 
 *     
 * @param[in] none 
 ******************************************************************************/
void refreshConfigurationWithBroker(){
  /* if the version number has changed, update the MQTT reports */
  if (prefs.getInt("version", 0) != VERSION_INT){
    bridge.instructServicePortToDisplayString(" UPDATING");
    bridge.publishMachineEntityConfigurations();
    bridge.publishMachineFunctionConfiguration(); 

    /* version stored*/
    prefs.putInt("version", VERSION_INT);
  }
}

/***************************************************************************//**
 * Update subscriptions for bridge events and device specific events.
 *
 * @param[out] none 
 *     
 * @param[in] none 
 ******************************************************************************/
void refreshSubscriptionsWithBroker(){
  bridge.subscribeToMachineFunctionButtonCommandTopics();
  bridge.subscribeToBridgeSubtopics();
}

/***************************************************************************//**
 * Connect to the mqtt broker. Called from the connection manager
 * loop. Once connected to mqtt, perform initial mqtt 
 *
 * @param[out] none 
 *     
 * @param[in] none 
 ******************************************************************************/
void connectToBroker(){

  /* semaphore-protected */
  bridge.instructServicePortToDisplayString("   MQTT   ");

  /* operaitonal state topic */
  char operational_state_topic[56]; 
  sprintf(
    operational_state_topic, 
    MQTT_ROOT "/%i/%i/%i", 
    JuraEntityConfigurations[0].machineSubsystemType, 
    JuraEntityConfigurations[0].subsystemAttributeType,
    0
  );

  /* set keepalive before connection attempt; design pattern from idahowalker on arduino forums */
  mqttClient.setKeepAlive( 90 );
  mqttClient.setServer(MQTTBROKER, 1883);
  mqttClient.setBufferSize(2048);       /* for receiving large recipes; discontinyed; not necessary? */

  while (! mqttClient.connected()){
    mqttClient.connect(TAG, MQTT_USER, MQTT_PASS, operational_state_topic, 0, false, "OFF" , true);
    vTaskDelayMilliseconds(2500);
  }

  mqttClient.setCallback( mqttCallback );

  /* subscriptions and mqtt first stuffs refreshing goes here */
  xSemaphoreWrappedSetBoolean(xMQTTStatusSemaphore, connectedToBroker, true);   
} 

/***************************************************************************//**
 * Connect to configured Wi-Fi network.
 *
 * @param[out] none 
 *     
 * @param[in] none 
 ******************************************************************************/
void connectToWiFiNetwork(){

  /* booting message on display */
  bridge.instructServicePortToDisplayString("   WIFI   ");

  /* configuration values*/
  WiFi.mode(WIFI_STA); 
  WiFi.persistent(true);

  int wifiConnectionAttempt = 0;
  while (WiFi.status() != WL_CONNECTED){
    wifiConnectionAttempt++;
    WiFi.disconnect();
    WiFi.begin( WIFINAME, WIFIPASS );
    vTaskDelayMilliseconds(5000);
    if ( wifiConnectionAttempt == 10 )
    {
      ESP.restart();
    }
  }
  WiFi.onEvent( WiFiEvent );
  
  /* print IP address for debugging - send to frontend?*/
  IPAddress localIP = WiFi.localIP();
  ESP_LOGI(TAG,"Wi-Fi: %i.%i.%i.%i",localIP[0], localIP[1],localIP[2],localIP[3]);
  xSemaphoreWrappedSetBoolean(xWIFIStatusSemaphore, connectedToNetwork, true);   
} 

/***************************************************************************//**
 * Task to maintain MQTT and Wi-Fi communicationns.
 *
 * @param[out] none 
 *     
 * @param[in] pvParameters required for callback
 ******************************************************************************/
void communicationsKeepAliveTask( void *pvParameters ){
  mqttClient.setKeepAlive(90);
  for (;;){
    if ( (wifiClient.connected()) && (WiFi.status() == WL_CONNECTED) && (mqttClient.connected()) ){
      xSemaphoreTake( xMQTTSemaphore, portMAX_DELAY );
      mqttClient.loop();
      xSemaphoreGive( xMQTTSemaphore );
    
    }else {
      /* mqtt cannot be available if wifi is not available */
      xSemaphoreWrappedSetBoolean(xMQTTStatusSemaphore, connectedToBroker, false);   
      xSemaphoreWrappedSetBoolean(xWIFIStatusSemaphore, connectedToNetwork, false);   

      if ( !(wifiClient.connected()) || !(WiFi.status() == WL_CONNECTED)){
        connectToWiFiNetwork();
      }

      connectToBroker();
      refreshSubscriptionsWithBroker();
      refreshConfigurationWithBroker();

      /* set ready */
      bridge.instructServicePortToSetReady();
    }
    vTaskDelayMilliseconds( 250);
  }

  /* null = calling task is deleted; should never exit this loop anyway...*/
  vTaskDelete ( NULL );
}
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
void loop() {}

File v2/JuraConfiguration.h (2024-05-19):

#ifndef JURACONFIGURATION_H
#define JURACONFIGURATION_H
#include "JuraEnums.h"

/* debugging and ressearch feature flags */
#define PRINT_UNHANDLED    false    /* print values that aren't curerntly captured; for investigation of new values and when they change*/
#define PRINT_KNOWN_VALUES false    /* for debugging, print captured values when recognized andupdated */

/* ESP */
#define BRIDGE_NAME       "Jura Bridge"
#define CONTROLLER_NAME   "Jura Controller"
#define THERMOBLOCK_NAME  "Jura Thermoblock"
#define BREW_GROUP_NAME   "Jura Brew Group"
#define WATER_NAME        "Jura Water System"
#define DOSING_NAME       "Jura Dosing System"
#define MILKSYSTEM_NAME   "Jura Milk System"

#define MQTT_ROOT     "jurabridge"
#define NAME_PREFIX   ""      /* trailing space strongly recommended if used */
#define ENTITY_PREFIX ""      /* trailing underscore required if used */
#define PREF_PREFIX   "PREF"
#define MANUFACTURER  "Andrew J Freyer"
#define MODEL_NUM     "jurabridge for Jura ENA Micro 90"
#define TAG           "jb"

/* jura service port and hardware interface configuration */
#define DEV_BOARD_ID                            "ESP32 Dev Module"
#define DEV_BOARD_UART_ID                       2
#define DEV_BOARD_LED_PIN                       2
#define DEV_BOARD_BUTTON_PIN                    21
#define DEV_BOARD_UART_RX_PIN                   16
#define DEV_BOARD_UART_TX_PIN                   17
#define DEV_BOARD_UART_TIMEOUT                  300

/* timeout values for force refresh */
#define JURA_MACHINE_EEPROM_TIMEOUT             3000000
#define JURA_MACHINE_INPUT_BOARD_TIMEOUT        3000000
#define JURA_MACHINE_HEATED_BEVERAGE_TIMEOUT    3000000
#define JURA_MACHINE_SYSTEM_CIRCUITRY_TIMEOUT   10000

/* timeout values for calculated properties */ 
#define JURA_MACHINE_BEANS_REFILLED_TIMEOUT           5000
#define JURA_MACHINE_DRAINAGE_TRAY_EMPTIED            5000

/* timeouts for machine operations */
#define JURA_MACHINE_AWAIT_NEXT_INSTRUCTION_TIMEOUT_S 120
#define JURA_MACHINE_AUTOMATIC_MAINTENANCE_TIMEOUT_S  120
#define JURA_MACHINE_AUTOMATIC_MILK_RINSE_TIMEOUT_S   150
#define JURA_MACHINE_AUTOMATIC_DISPENSE_LIMIT_TIMEOUT_S 90
#define JURA_MACHINE_AUTOMATIC_BREW_GROUP_RINSE_TIMEOUT_S 300

/* preference keys */
#define PREF_KEY                                "jb"

/* temperature thresholds */
#define COLD_MODE_THRESHOLD                     60
#define LOW_MODE_THRESHOLD                      94  /* if we're super low, the thremoblock heats up too fast and goes up to 80 deg c for water dispense */
#define HIGH_MODE_THRESHOLD                     105
#define OVERTEMP_THRESHOLD                      115
#define SANITATION_TEMP_THRESHOLD               148 /* for milk clean; required temperature is 150, so 2deg buffer*/
#define OVEREXTRACTION_THRESHOLD                110
#define UNDEREXTRACTION_THRESHOLD               85


/* constants */
#define JURA_MACHINE_BEAN_HOPPER_CAPACITY_G      200
#define JURA_MACHINE_DRAINAGE_TRAY_CAPACITY_ML   900 /* actual Drainage Tray capacity measured at 500ml (which is half this value), but it appears warnings trigger at 900 raw value*/
#define JURA_MACHINE_WATER_RESERVOIR_CAPACITY_ML 1000
#define BREW_GROUP_CLEAN_THRESHOLD               130
#define BREW_GROUP_CLEAN_RECOMMEND_THRESHOLD     100
/* 
pumped water volume will vary vary each dispense type; excess will remain in the machine or will 
be dumped to the drainage tray (e.g., condenser, drainage valve, etc). the following are approximations;  
*/
#define DISPENSED_ML_CALIBRATION_COEFFICIENT_DEFAULT   0.5        /* 0.46391753 dispensed 90 ml when 194 was reported; 0.5 presumes 0.5ml for every spin of the flow meter */
#define DISPENSED_ML_CALIBRATION_COEFFICIENT_COFFEE    0.44978166 /* dispensed 206 ml when 458 was reported */
#define DISPENSED_ML_CALIBRATION_COEFFICIENT_ESPRESSO  0.35802469 /* dispensed 29 ml when 81 was reported */
#define DISPENSED_ML_CALIBRATION_COEFFICIENT_MILK      2.17543860  /* dispensed 124 ml when 57 was reported */
#define DISPENSED_ML_CALIBRATION_COEFFICIENT_OATMILK   2.08196721  /* dispensed 127 ml when 61 was reported */

#define BUTTON_HOLD_DURATION_MS                        750
/*

  name:         JuraEntityConfigurations
  type:         array
  description:  this array contains instances of JuraEntityConfiguration; 
                indexes of this array are used to store values in caches for machine instance
                and bridge instance. 

*/

/*

    NOTE: THE MORE OF THESE THAT ARE ENABLED AND ARE REPORTING, THE SLOWER THE ENTIRE SYSTEM 
    WILL BE, INCLUDING TO RESPOND TO MQTT INSTRUCTIONS FROM HA OR ANOTHER CONTROLLER. STRONGLY RECOMMEND 
    DISABLING MANY OF THE SENSORS IF THEY'RE NOT NEEDED IN HOME AUTOMATION PLATFORMS.

*/
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

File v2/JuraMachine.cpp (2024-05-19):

#include "JuraBridge.h"
#include "JuraMachine.h"

/* set poll rates */
#define POLL_MEMORY     -1
#define POLL_DUTY_FULL  1
#define POLL_DUTY_50    2
#define POLL_DUTY_33    3
#define POLL_DUTY_20    5
#define POLL_DUTY_15    7
#define POLL_DUTY_10    11
#define POLL_DUTY_5     23
#define POLL_DISABLED   101

JuraMachine::JuraMachine(JuraBridge& bridge, SemaphoreHandle_t &xMachineReadyStateVariableSemaphoreRef) :  _bridge(&bridge), xMachineReadyStateVariableSemaphore(xMachineReadyStateVariableSemaphoreRef) {

  /* semaphore for dispense limit setting */
  xDispenseLimitSemaphore = xSemaphoreCreateBinary();
  xSemaphoreGive( xDispenseLimitSemaphore);

  /*eeprom*/
  _rt0.setCommand(JuraServicePortCommand::RT0);
  _rt1.setCommand(JuraServicePortCommand::RT1);
  _rt2.setCommand(JuraServicePortCommand::RT2);

  /* testing */
  _rt3.setCommand(JuraServicePortCommand::RT3);
  _rt4.setCommand(JuraServicePortCommand::RT4);
  _rt5.setCommand(JuraServicePortCommand::RT5);
  _rt6.setCommand(JuraServicePortCommand::RT6);
  _rt7.setCommand(JuraServicePortCommand::RT7);
  _rt8.setCommand(JuraServicePortCommand::RT8);
  _rt9.setCommand(JuraServicePortCommand::RT9);
  _rtA.setCommand(JuraServicePortCommand::RTA);
  _rtB.setCommand(JuraServicePortCommand::RTB);
  _rtC.setCommand(JuraServicePortCommand::RTC);
  _rtD.setCommand(JuraServicePortCommand::RTD);
  _rtE.setCommand(JuraServicePortCommand::RTE);
  _rtF.setCommand(JuraServicePortCommand::RTF);


  /* input board and controller */
  _ic.setCommand(JuraServicePortCommand::IC);

  /* heated beverage */
  _hz.setCommand(JuraServicePortCommand::HZ);
  
  /* system circuitry  */
  _cs.setCommand(JuraServicePortCommand::CS);
  
  /* system memory locations  */
  //_rm00.setCommand(JuraServicePortCommand::RM00);

  /* known ignores */
  _cs.setBinIndexIgnore(SUBSTR_BIN_INDEX_UNKNOWN_MACHINE_CONFIGURATION_GROUP_1, 10);
  _cs.setBinIndexIgnore(SUBSTR_BIN_INDEX_UNKNOWN_MACHINE_CONFIGURATION_GROUP_2, 10);
  _cs.setBinIndexIgnore(SUBSTR_BIN_INDEX_UNKNOWN_MACHINE_CONFIGURATION_GROUP_3, 10);
  _cs.setBinIndexIgnore(SUBSTR_BIN_INDEX_UNKNOWN_MACHINE_CONFIGURATION_GROUP_4, 10);
  _cs.setBinIndexIgnore(SUBSTR_BIN_INDEX_UNKNOWN_MACHINE_CONFIGURATION_GROUP_5, 10);
    
  /*
    NOTES:
      unknown_machine_configuration_group_1 = 0; // brew group moving??
      unknown_machine_configuration_group_2 = 0; // beginning of water 1 -> 0 (1.5) seconds
      unknown_machine_configuration_group_3 = 0; // output valve encoder state 
      unknown_machine_configuration_group_4 = 0; 
      unknown_machine_configuration_group_5 = 0; // brew group ??? 
  */

  /* meta state */
  states[(int) JuraMachineStateIdentifier::OperationalState] = (int) JuraMachineOperationalState::Starting;
  states[(int) JuraMachineStateIdentifier::ReadyStateDetail] = (int) JuraMachineReadyState::ExecutingOperation;

  /* fill operational state history */
  for (int i = 0; i < MAX_STATE_EVENT_HISTORY ; i++) {
    operationalStateHistory[i] = (int) JuraMachineOperationalState::Starting;
    dispenseHistory[i] = 0;
    flowRateHistory[i] = 0;

    temperatureAverageHistory[i] = 0;
    temperatureMaximumHistory[i] = 0;
    temperatureMinimumHistory[i] = 0;
  }

  /* set to zero  */
  for (int i = 0; i < MAX_DISPENSE_SAMPLES ; i++) {
    flowRateSamples[i] = 0;
    temperatureSamples[i] = 0;
  }

  /* init to starup */
  operationalStateHistory[0] = (int) JuraMachineOperationalState::Starting;
}

/***************************************************************************//**
 * Leverage an array as a linked list or queue
 *
 * @param[out] null 
 *     
 * @param[in] int arr[]
 * @param[in] int size
 * @param[in] int newValue
 ******************************************************************************/
 void JuraMachine::pushElement(int arr[], int size, int newValue) {
    if (size <= 0)
        return; // Nothing to shift

    // Shift each element one position to the right
    for (int i = size - 1; i > 0; --i) {
        arr[i] = arr[i - 1];
    }

    // Set the first element with the new value
    arr[0] = newValue;
}

/***************************************************************************//**
 * Force an input int to fall within a particular range
 *
 * @param[out] int 
 *     
 * @param[in] int inlogg
 * @param[in] int min
 * @param[in] int max
 ******************************************************************************/
 int JuraMachine::filteredLong(int inlong, int min, int max){
  if (inlong < min){return min;} if (inlong > max){return max;}
  return inlong;
}

/***************************************************************************//**
 * Receives input of a new sample of a memory line from the Jura and outputs a bool
 * indicating whether a portion of that line has changed. 
 *
 * @param[out] bool 
 *     
 * @param[in] JuraMemoryLine *memoryLine,
 * @param[in] int *value, 
 * @param[in] int value_index, 
 * @param[in] int min_val
 * @param[in] int max_val
 ******************************************************************************/
 bool JuraMachine::didUpdateJuraMemoryLineValue(
  JuraMemoryLine *memoryLine,
  int *value, 
  int value_index, 
  int min_val, 
  int max_val){

  if (memoryLine->hasUpdateForIntegerValueOfServicePortResponseSubstringIndex(value_index)){
    *value = filteredLong(
      (int) memoryLine->checkIntegerValueOfServicePortResponseSubstringIndex(value_index), 
      min_val, 
      max_val);

    return true;
  }
  return false;
}

/***************************************************************************//**
 * Receives input of a new sample of a control board service port call and outputs
 * a bool indicating whether a portion of that output has changed. 
 *
 * @param[out] bool 
 *     
 * @param[in]   int *value, 
 * @param[in]   int value_index, 
 * @param[in]   int bits, 
 * @param[in]   JuraInputBoardBinaryResponseInterpretation _invert
 ******************************************************************************/
 bool JuraMachine::didUpdateJuraInputControlBoardValue(
  int *value, 
  int value_index, 
  int bits, 
  JuraInputBoardBinaryResponseInterpretation _invert) {
  /* check for update, if update set value at passed pointer */
  if (_ic.hasUpdateForValueOfServicePortResponseSubstringIndex(value_index, bits)){
    int raw = (int) _ic.returnValueOfServicePortResponseSubstringIndex(value_index, bits);
    *value = (_invert == JuraInputBoardBinaryResponseInterpretation::Inverted) ? (!(bool) raw) : (int) raw;
    return true;
  }
  return false;
}
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

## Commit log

2023-05-04 Refresh tracked files
    [jurabridge-diffuser.3mf]
2023-05-07 update for displayfixing
    [configuration.h]
2023-05-16 0.4.5
    Powder operations, custom menu from input button
    [configuration.h]
2024-05-07 v2 commit
    [configuration.h]
